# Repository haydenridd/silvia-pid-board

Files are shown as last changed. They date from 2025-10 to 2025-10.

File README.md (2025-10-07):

# Rancilio Silvia PID Board

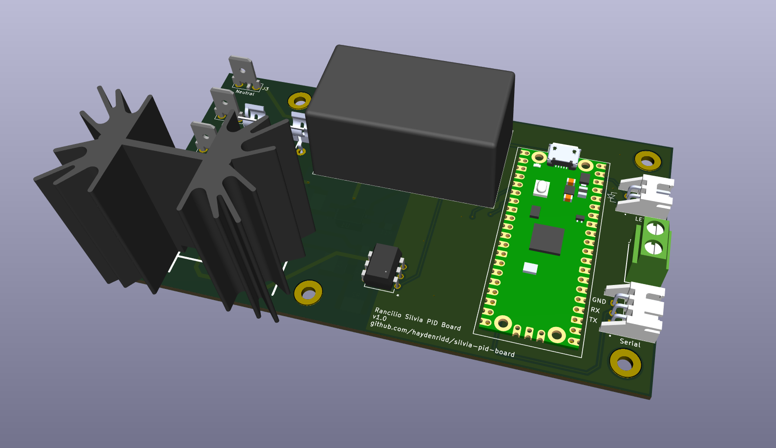
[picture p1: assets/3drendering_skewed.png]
rendering


A hardware and firmware project for adding PID boiler control to a stock Rancilio Silvia espresso machine.

## Obligatory Disclaimer

This project involves working with mains voltage as well as high power output heaters! Mains voltage *can kill or
seriously injure you* and improper control of an ~850W heating element *can start fires*. This project is provided
as-is with no regulatory certifications or guarantees of safety. It is on the user to do their due diligence in
ensuring their own safety, as well as the safe modification and operation of the espresso machine.

## Motivation

Adding PID heater control to the Rancilio Silvia is a popular mod, however it usually involves adding a
standalone PID controller like [this](https://www.auberins.com/index.php?main_page=product_info&products_id=36) to the
exterior of the machine. I've also seen a
number of great write-ups on home-brew mods \(so to speak\) like [this](https://misssilviapi.wordpress.com/) and
[this](https://int03.co.uk/blog/project-coffee-espiresso-machine/). However, many of the mods have
gravitated towards using various parts and modules found on Amazon, and are generally fairly invasive to the machine
itself (modules on the outside, cutting into the chassis, etc).

I had two goals with this project:
- Design a robust PID control board and source components entirely from a reputable distributor (DigiKey in this case)
- Design the board in such a way that it fits inside the machine, and leaves the control of the machine unchanged

### A Brief Aside on Amazon Parts
At the time of this writing, the electrical engineer in me would *not* consider Amazon to be a reputable retailer
for electronic parts. There have been many [reports](https://www.coffeeforums.co.uk/threads/gaggia-classic-pid-owners-watch-out-for-counterfeit-ssrs-on-ebay-amazon-etc.61314/)
of [fake parts](https://squashpractice.com/2024/01/01/counterfeits-parts-ebay-scammers-and-amazon-shills/) coming from
Amazon across all corners of industry. While these are generally ~half the price of the part they're
knocking off, you have essentially no recourse or accountability should this part fail in a catastrophic way. And
when it comes to switching AC mains and high powered heaters, that was not a gamble I was willing to take. This
project sources its parts entirely from DigiKey with the exception of a custom RTD sensor for the boiler.

## Design Ethos

I love the chunky, tactile feel of the stock Silvia machine. I wanted to leave how you control the machine entirely
unchanged. This is NOT a total conversion mod like the [Gagguino](https://gaggiuino.github.io/#/) although that project
is certainly cool. Post-mod, the machine still looks and functions largely the same to the external user, with a
small exception being how I use the heating lamp to indicate temperature status.

## Hardware Design

See [the hardware README](./silvia_pid_board/README.md) for a detailed breakdown of the electronic design, parts list,
and hookup diagram. This diagram shows the high-level design of the board:

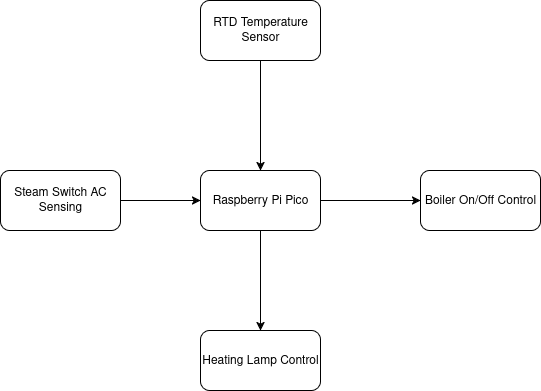
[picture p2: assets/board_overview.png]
board_overview


The board, in a hacky chip board "enclosure", fits snugly in between the steam valve and the leftmost control switches:
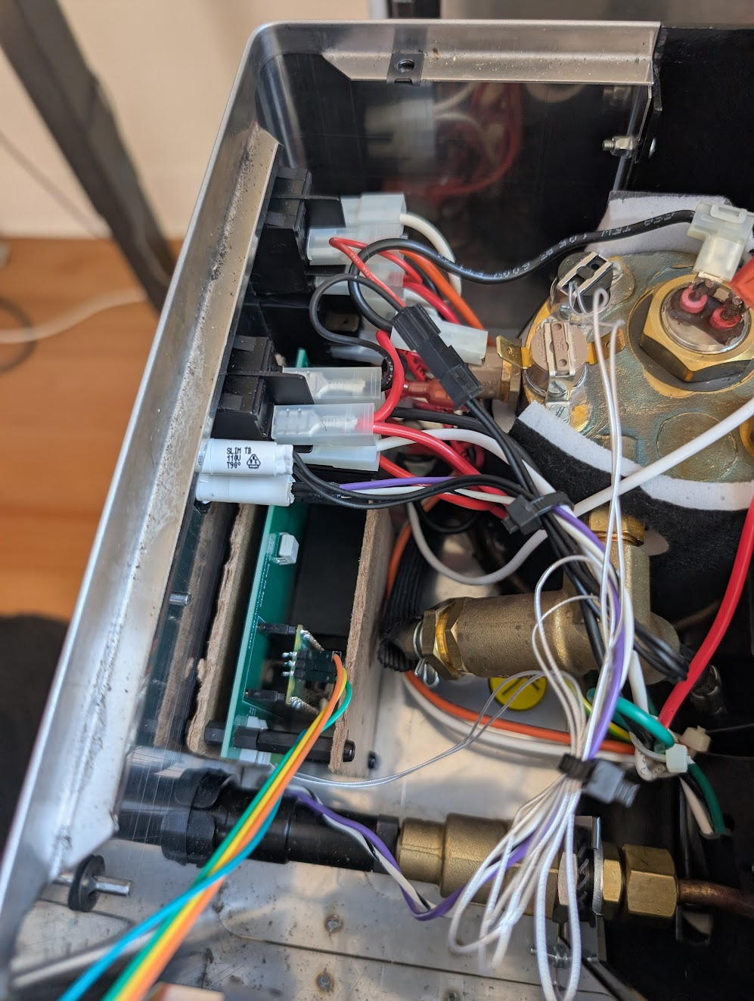
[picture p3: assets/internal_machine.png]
internal_machine


## Firmware Design

A Raspberry Pi Pico was used for the microcontroller driving the hardware because they're cheap, and extremely well
documented. The firmware is written in [Zig](https://ziglang.org/), a fantastic up-and-coming language that I've
fallen in love with for low-level firmware development. See [the firmware README](./firmware/README.md) for more
details.

## Performance

The following shows the temperature behavior of the thermostat style regulation that comes with a stock Silvia. 

A graph of temperature over time at the espresso temperature setpoint:

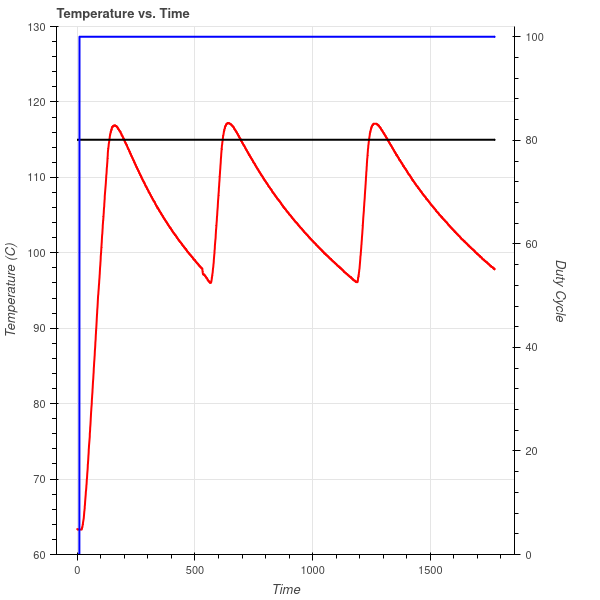
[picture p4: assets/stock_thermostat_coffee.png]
stock_coffee


And a graph of temperature of time at the steam temperature setpoint:

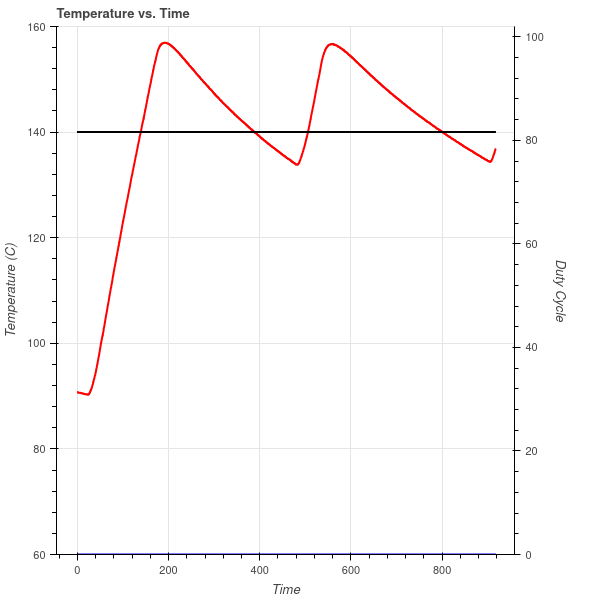
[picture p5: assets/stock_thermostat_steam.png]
stock_steam


Compare this to the new PID regulation at the espresso setpoint:

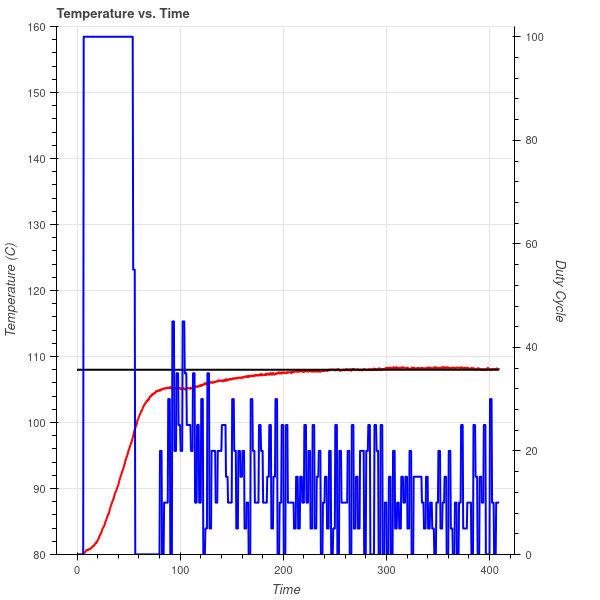
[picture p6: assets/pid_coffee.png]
pid_coffee


And regulation at the steam setpoint:

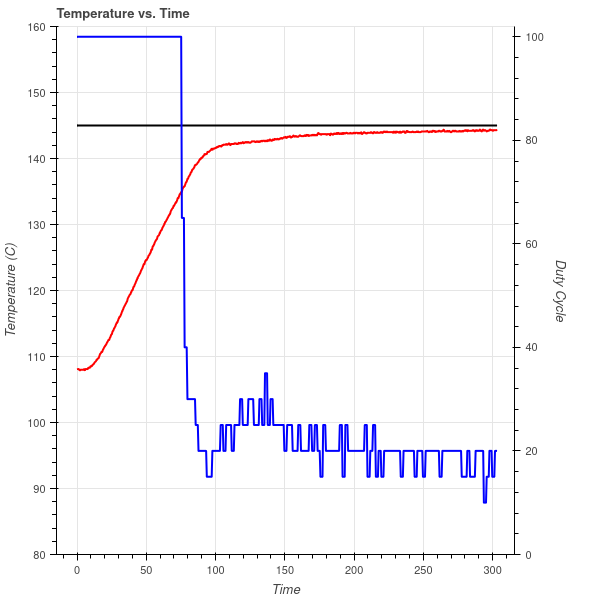
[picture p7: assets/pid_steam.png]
pid_steam


Where the red line is temperature, and the blue line is duty cycle of the heater. Both of these plots can be produced
with a [script](firmware/scripts/graph_temperature.py) in the firmware folder. See that README for more details on
data logging + plotting.

Espresso setpoint regulation is extremely tight, generally regulating to within 1C. Steam regulation generally sits
~2C below the setpoint of 145C, but experimentally I found this to produce nice milk steaming pressure. Both setpoints were chosen based
on the behavior of the original thermostat + some experimental tweaking. It should be noted temperature is measured
at the exterior of the boiler, meaning a setpoint of 108C does *not* mean 108C water is going through your
espresso puck. 

## Building Your Own

All the tools you need to make one of these modules yourself are provided in this repository. I used JLPCB to build the
boards, however the gerber files located in `silvia_pid_board/board_gerbers` can be used to build boards at a PCB
fab of your preference. Note though that design rules were checked according to JLPCB's capabilities. The KiCAD design
files are also available in `silvia_pid_board` should you want to modify the board or run different design rule checks.

At the time of writing, the total BOM cost of the Digikey parts is $34. Should you choose to use the same RTD module
costing $28, and JLPCB for your fab costing ~$30 with shipping, and add some cash for shipping from Digikey, the total
cost sits ~$100 for a buildout of this. Pretty good considering an off the shelf module is ~$150! I've included the 
Digikey part numbers with the [parts list](./silvia_pid_board/parts_list.csv) where relevant, so ordering parts for
this build should be fairly straightforward.

## Closing Thoughts and Areas of Improvement

This repo is unlikely to see any major updates, and mostly serves as a write-up/how-to for anyone looking to replicate
or expand upon this project. In its current state, it does exactly what I want for my machine. However, here are some
minor things I would change if I were to do another revision of the board/firmware:
- Add a standardized SWD header to the board + route corresponding signals from the Pico for easier debugger
connection
- Solder the RP2040 + required supporting ICs directly to the board to save space rather than using the Pico board
- Add CAD designs for a 3D printable enclosure
- Implement a serial port via a USB endpoint, removing the need for a dedicated UART connection
- Expand on the CLI and logging capabilities

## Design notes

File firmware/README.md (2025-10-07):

# PID Control Firmware

The following describes the firmware running on the Rpi Pico that implements PID control for the heater.

## Zig

The firmware is written in the [Zig](https://ziglang.org/) programming language, and currently tracks version `0.15.1`.
It uses the [MicroZig project](https://microzig.tech/) to provide a HAL and build utilities for the RP2040, a project
which I also contribute to!

## Building + Flashing

Installing Zig is required to build firmware. Once installed, build firmware by running `zig build` in this directory.
You will see two artifacts in `zig-out`. The `.elf` file can be flashed to the Pico over the SWD interface using a
debugger. There is an [example script](scripts/flash_fw.sh) that shows how this is accomplished with a JLink. The `.uf2`
file can be transferred to the Pico connected to a computer when it's in mass storage mode.

By default, the build occurs in debug mode. To build at higher optimization levels see `zig build -h`. 

## Architecture

The code follows a "super loop" architecture, with code seperated into modules that are given cpu time with the naming convention
`doWork()` as a method. Technically, this is known as "co-operative multitasking with static priority", where each module can't
get CPU cycles until the previous module yields control. The order in the loop each module is called can be thought
of as the "priority".

Examine the code for more details, but the high level modules are briefly described below.

### `Blink`

Blinks the on-board LED of the Pico at a fixed interval, as a sanity check that firmware hasn't crashed.

### `DataLogger`

Outputs CSV data points to a UART port for logging.

### `TemperatureRegulation`

Performs the PID control loop given regular temperature measurements from the RTD sensor. Setpoint is changed according to whether the steam switch is active or not.

### `RtdMeasurement`

Handles fetching temperature readings from the MAX31865 chip.

### `Cli`

Implements a rudimentary CLI for controlling firmware as it runs. Currently uses [RTT](https://kb.segger.com/RTT), however it is
designed in a way to take a generic `std.Io.Reader` as its input
source. A fun example of `comptime` usage to cut down on code repetition.

### `HeaterIndicator`

Controls the heater indicator LED using PWM. Currently it only has three states:
- Solid on: temperature is far enough away from target such that the boiler is turned on 100%
- Pulsing on: temperature is within a threshold to where PID is bringing temperature closer to target
- Solid off: Temperature is within 2C of target

Note that "solid on" still isn't at 100% duty cycle. I experimentally determined a nice value that seemed to match the brightness of the other lamps on the machine.

### `irq`

A special module that isn't "given work" like other modules, because
it entirely executes in interrupt handlers. Interrupts are used to
handle detecting regular zero crossing events on the pin that senses
whether or not the steam switch is turned on.

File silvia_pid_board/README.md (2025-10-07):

# Hardware Design

The following outlines:
- Board circuit design
- Hookup/wiring guide
- Board mounting
- BOM/Fabrication info

## Circuit Design

A PDF of the board schematic can be found [here](./silvia_pid_board.pdf), and is useful for following along with
circuit design discussion. The circuit design for this board can be broken into the following components:
- Power supply
- AC mains switching for the boiler
- AC mains detection from the steam switch
- Heating LED control

Note that this PCB was designed with a 120VAC/60Hz mains supply in mind, and that a careful design review should be
conducted if a user wants to adapt this to a different mains input (for instance 220VAC).  

### Power Supply

Extremely simple and easy, as it is a single component, the [IRM-05](https://www.meanwellusa.com/upload/pdf/IRM-05/IRM-05-spec.pdf).
While you could probably design a switched power supply that produces 5V from AC mains voltage for a little cheaper (this part costs $7),
this part simplified a lot of headaches. Does exactly as advertised, produces a clean 5V DC from 120 VAC delivering up
to 5W of power.

### AC Mains Switching

I spent the most time and intention on this part of the design, and switching AC to the boiler (to heat it) is
accomplished with the following circuit:
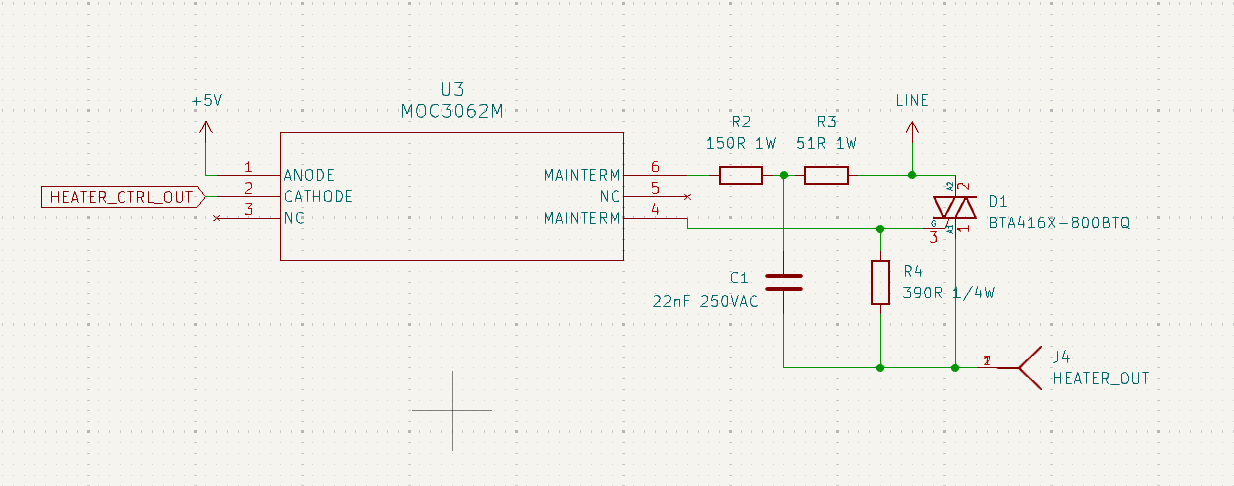
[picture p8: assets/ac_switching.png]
switching circuit


This was carefully designed based on the [following application note](https://www.st.com/resource/en/application_note/an5114-controlling-a-triac-with-a-phototriac-stmicroelectronics.pdf)
from ST Micro. I will be the first to admit it's over-engineered, as it almost certainly doesn't need a snubber circuit
given it's a simple resistive load being switched. One should note that the opto-coupler used is zero-crossing, meaning
no matter when the MCU goes to switch the heater on/off, it will only switch at the zero crossing point of the AC waveform.
Note you can only switch the heater on/off as fast as the frequency of the AC input (60Hz for US), however given the
duty period of the control loop is slow (one second) it doesn't matter.

The triac used for switching is passively cooled using a board mounted heatsink. Note that experimentally this has
been plenty effective for dissapating heat, but that a redesign is likely in order if switching a higher power heater
than the Silvia's.

### AC Mains Detection

This was entirely in service of allowing the steam switch to still turn on its own integrated AC powered lamp when it
switches on/off. The following circuit:
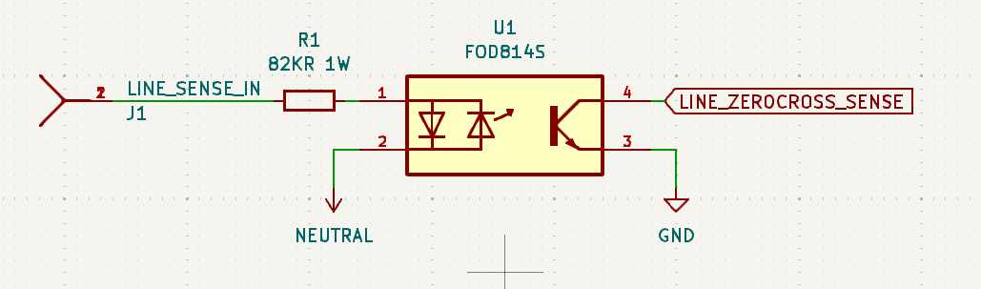
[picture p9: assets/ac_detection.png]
detection_circuit


Detects when the steam switch has been flipped "on" by detecting an AC signal. The [FOD814S](https://www.onsemi.com/download/data-sheet/pdf/fod814-d.pdf)
makes this quite easy. The `LINE_ZEROCROSS_SENSE` signal will end up being pulled to ground every time the AC signal
is over the turn-on voltage of the in-package photo-diodes. See the [firmware README](../firmware/README.md) for more
details on how this signal is used.

### Heating LED Control

The lower lamp on the power switched that is used as a heating indicator in the stock Silvia is replace by a white LED
controlled by the microcontroller. The dimensions of the chosen LED are quite similar to the stock lamp, so it was quite
easy to replace the stock lamp while preserving its housing and orange jewel lens. See the [firmware README](../firmware/README.md)
for more info on how this is used, but the general idea is a solid LED means "off target", a pulsing LED means
"close to target", and an off LED means "at target". 

## Hookup/Wiring Guide

The following is an annotated version of the electrical diagram provided with the Silvia's manual. It shows which
electrical connections have been removed or re-routed, and which signals they connect to on the PCB.
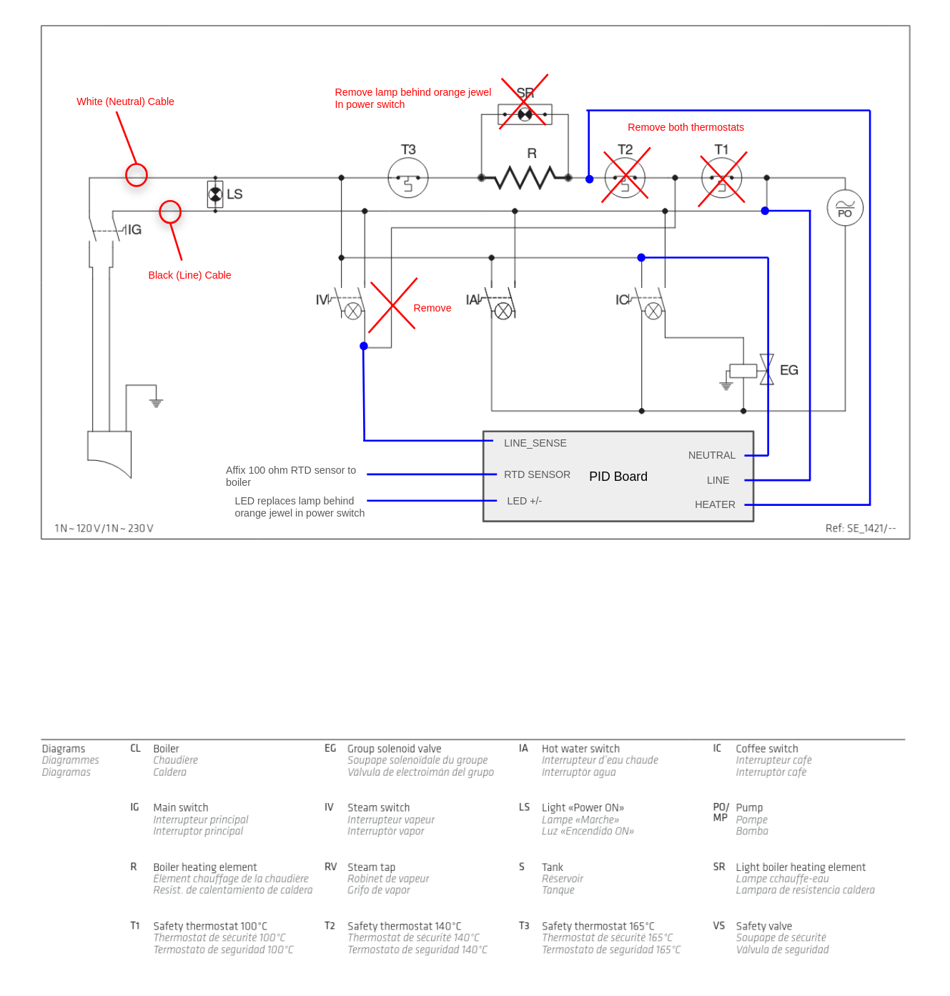
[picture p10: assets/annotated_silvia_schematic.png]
annotated_silvia_schematic


18 gauge wire was used for all AC signal level connections, and 22 gauge wire was used for all MCU signal
level connections (RTD sensor and LED).

## Board Mounting + Enclosure

Mounting holes are provided in the PCB to accomodate M3 size screws. I ended up using nylon standoffs and screws to
sandwich the board between two pieces of thick card-stock like material. 

## BOM/Fabrication

See [the following CSV](./parts_list.csv) for a full parts list for the project. The "Notes" column details whether the part goes on the
board itself, or is an ancillary part used for connections/etc.

The gerber files for getting this board fabricated are located in [board_gerbers](./board_gerbers), and pass the design
rules in `silvia_pid_board.kicad_dru` (provided by JLPCB).

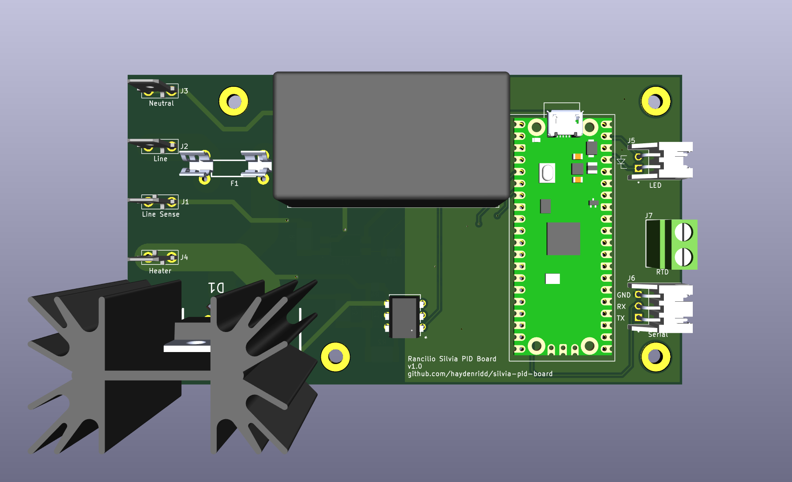
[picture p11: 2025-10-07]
assets/3drendering_top.png

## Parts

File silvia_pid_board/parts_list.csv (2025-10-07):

Reference | Value | Qty | DIGIKEY_PN | Notes
C1 | 22nF 250VAC | 1 | 399-CAN17C223KARACTUCT-ND | Board Component
C2,C3,C4 | 0.1uF | 3 | 311-1140-1-ND | Board Component
D1 | BTA416X-800BTQ | 1 | 1740-BTA416X-800BTQ-ND | Board Component
D1 | Heatsink | 1 | HS403-ND | Board Component
F1 | Fuse Holder | 1 | 36-3521-ND | Board Component
F1 | Fuse | 1 | 0225010.MXP-ND | Board Component
FB1 | FERRITE-0805NO | 1 | 490-1053-1-ND | Board Component
J1 | LINE_SENSE_IN | 1 | A29938CT-ND | Board Component
J2 | LINE_IN | 1 | A29938CT-ND | Board Component
J3 | NEUTRAL_IN | 1 | A29938CT-ND | Board Component
J4 | HEATER_OUT | 1 | A29938CT-ND | Board Component
J5 | S2B-XH-A | 1 | 455-S2B-XH-A-ND | Board Component
J6 | S3B-XH-A | 1 | 455-S3B-XH-A-ND | Board Component
J7 | 691137710002 | 1 | 732-10955-ND | Board Component
R1 | 82KR 1W | 1 | 13-RC2512JK-0782KLCT-ND | Board Component
R2 | 150R 1W | 1 | 13-SR2512JK-07150RLCT-ND | Board Component
R3 | 51R 1W | 1 | 13-AC2512JK-0751RLCT-ND | Board Component
R4 | 390R 1/4W | 1 | 311-390ERCT-ND | Board Component
R5 | 100R 1/4W | 1 | 311-270ERCT-ND | Board Component
R6,R8 | 100KR | 2 | 311-100KARCT-ND | Board Component
R7,R9,R12,R13,R14 | 10KR | 5 | 311-10KARCT-ND | Board Component
R10 | 270R 1/4W | 1 | 311-270ERCT-ND | Board Component
R11 | 6.2KR 1/4W | 1 | 311-6.2KERCT-ND | Board Component
R15 | 430Ω 0.1% | 1 | YAG1896CT-ND | Board Component
U1 | FOD814S | 1 | FOD814S-ND | Board Component
U2 | IRM-05-5 | 1 | 1866-3027-ND | Board Component
U3 | MOC3062M | 1 | MOC3062M-ND | Board Component
U4 | RASPBERRY_PI_PICO | 1 | 2648-SC0917-ND | Board Component
U5 | MBT3904DW1T1G | 1 | MBT3904DW1T1GOSCT-ND | Board Component
U6 | MAX31865AAP_ | 1 | MAX31865AAP+-ND | Board Component
~ | https://www.auberins.com/index.php?main_page=product_info&products_id=211 | 1 | ~ | Custom RTD sensor that fits in thermostat clip
~ | XHP-2 | 1 | 455-2266-ND | 2 position connector for RTD sensor port
~ | XHP-3 | 1 | 455-2219-ND | 3 position connector for UART port
~ | 2-520263-2 | 4 | A27821CT-ND | AMP connectors for connecting AC signals to board
~ | PPPC201LFBN-RC | 2 | S7053-ND | Female headers for Rpi Pico
~ | SXH-001T-P0.6N | 5 | 455-4220-100-ND | Crimp connectors
~ | INL-3AW30 | 1 | 1830-1006-ND | White LED for temperature lamp indicator replacement

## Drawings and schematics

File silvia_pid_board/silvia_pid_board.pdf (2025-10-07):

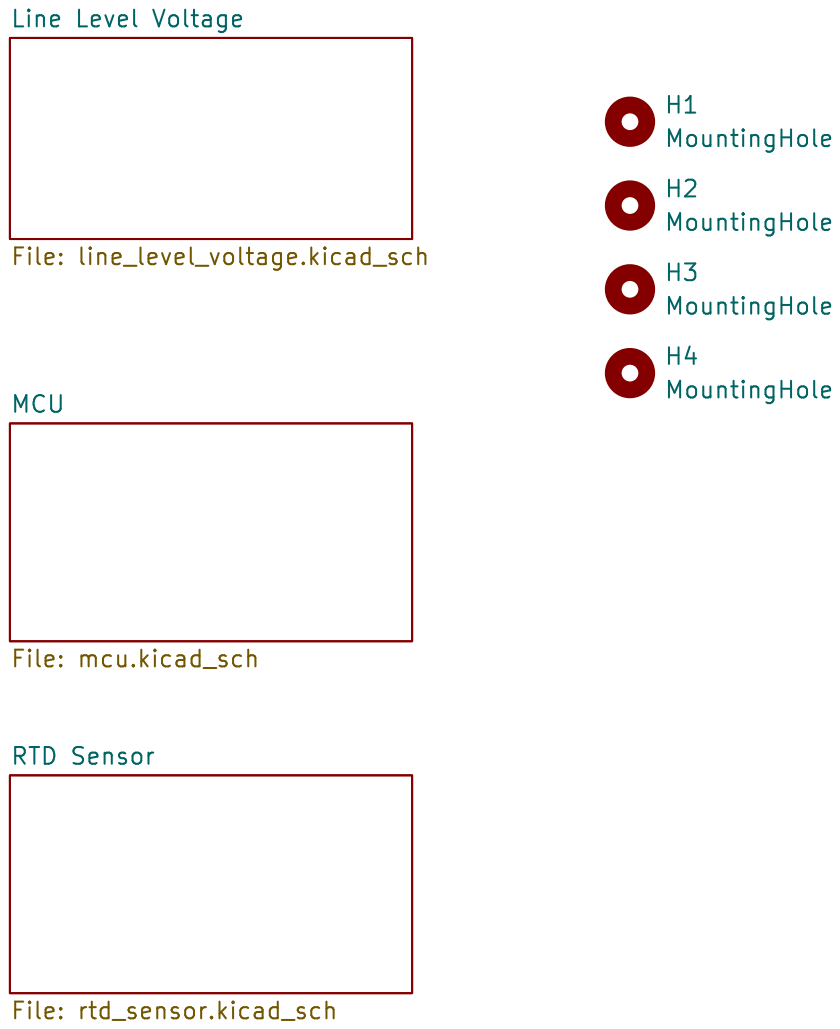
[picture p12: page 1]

Line Level Voltage File: line_level_voltage.kicad_sch RTD Sensor File: rtd_sensor.kicad_sch MCU

File: silvia_pid_board.kicad_sch Sheet: /
Id: 1/4 Title: Rancilio Silvia PID Board

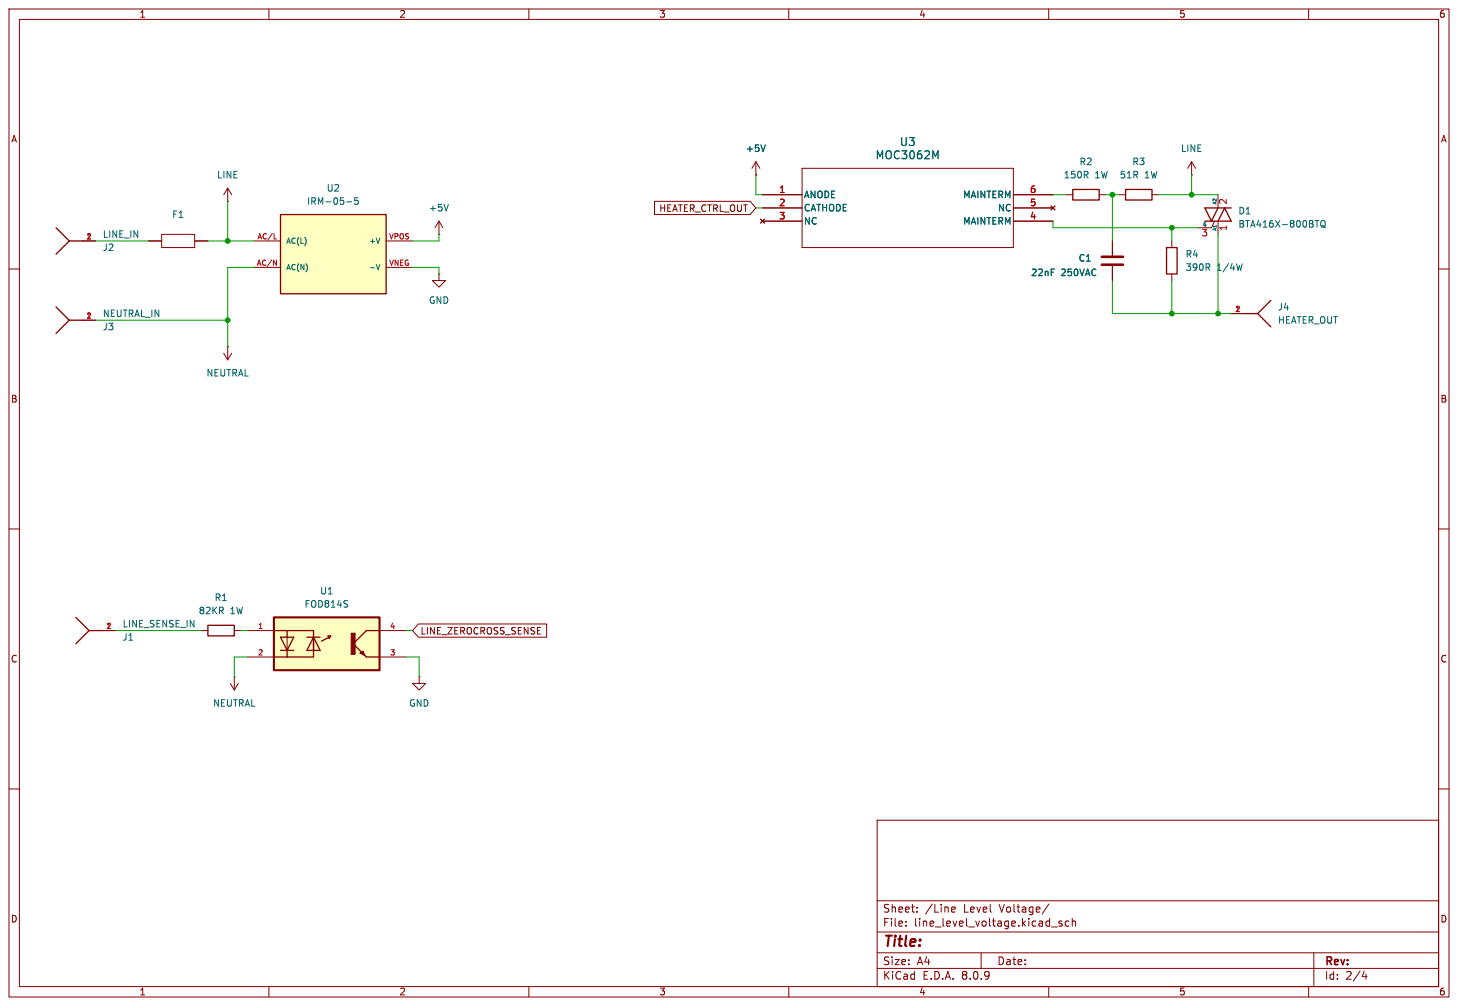
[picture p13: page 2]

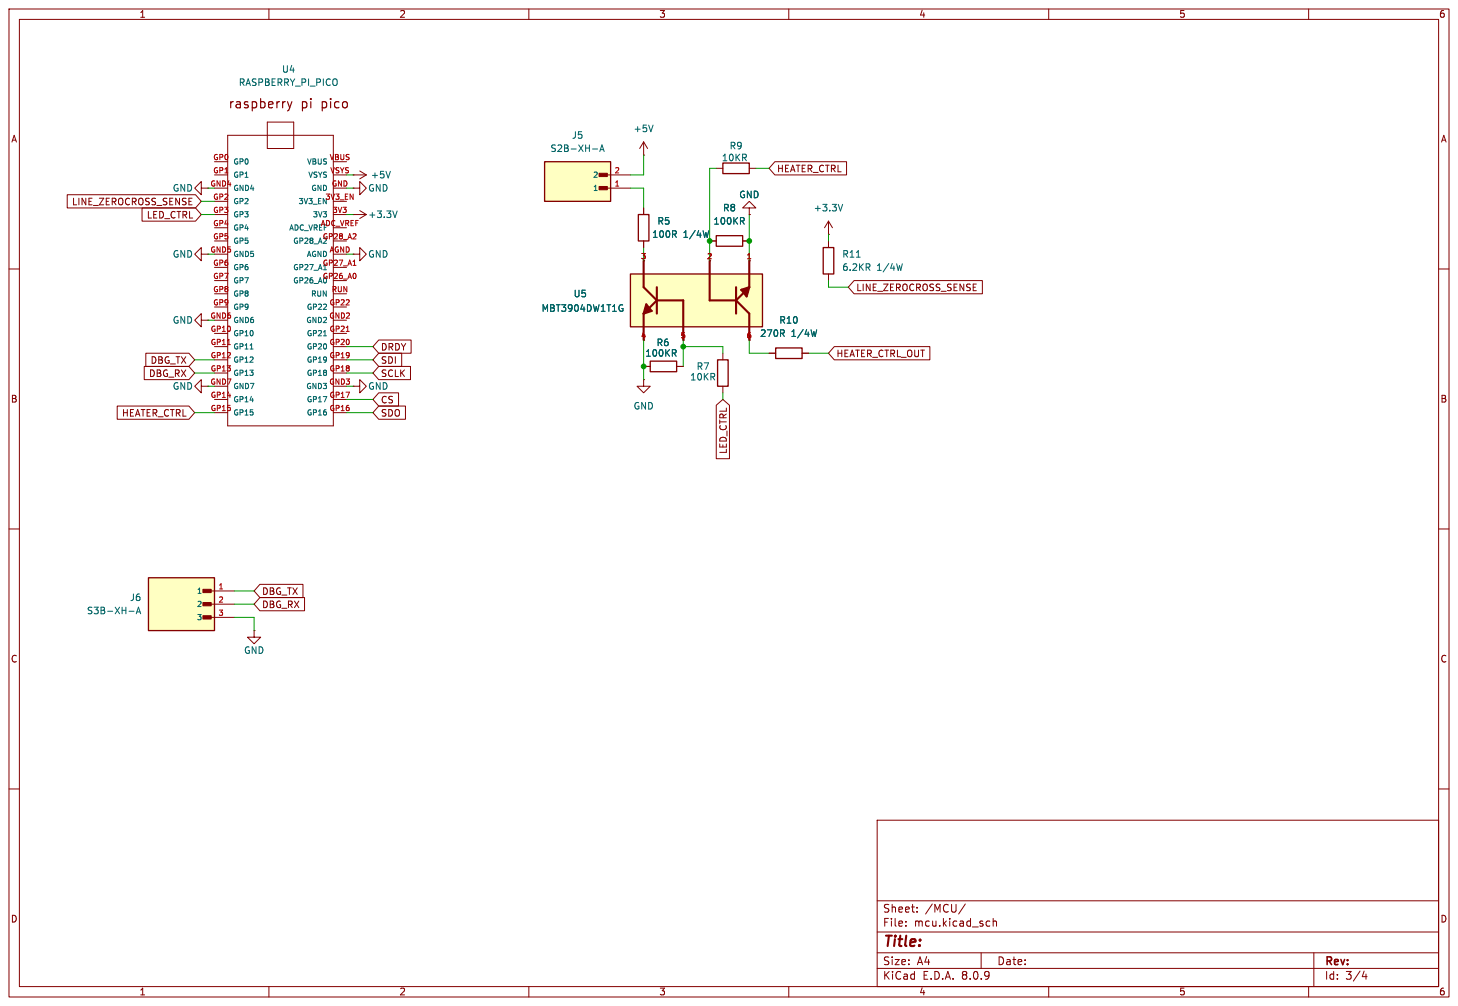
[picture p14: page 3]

Id: 3/4 Title: File: mcu.kicad_sch Sheet: /MCU/

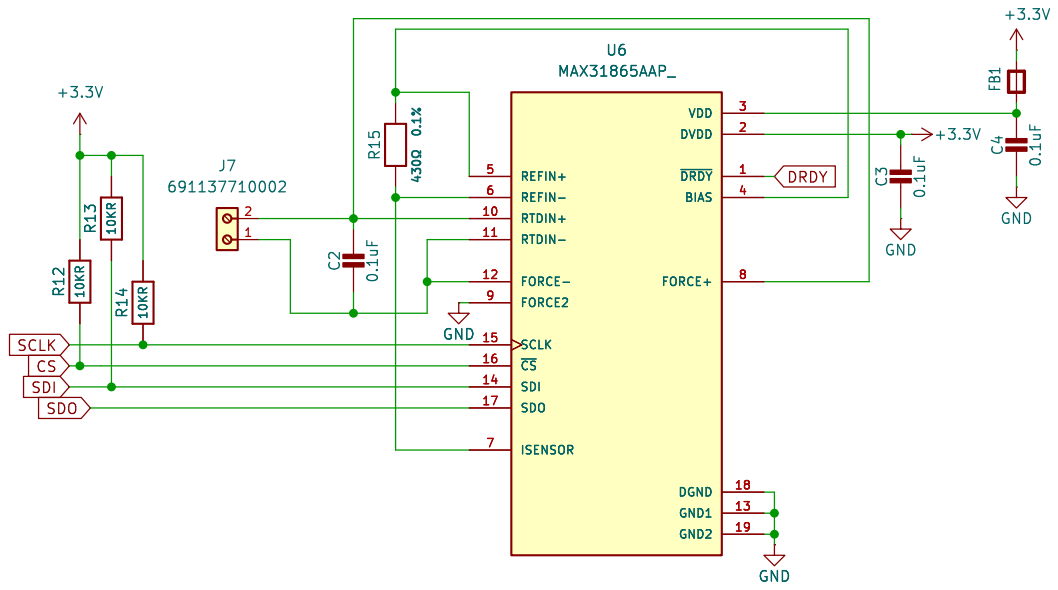
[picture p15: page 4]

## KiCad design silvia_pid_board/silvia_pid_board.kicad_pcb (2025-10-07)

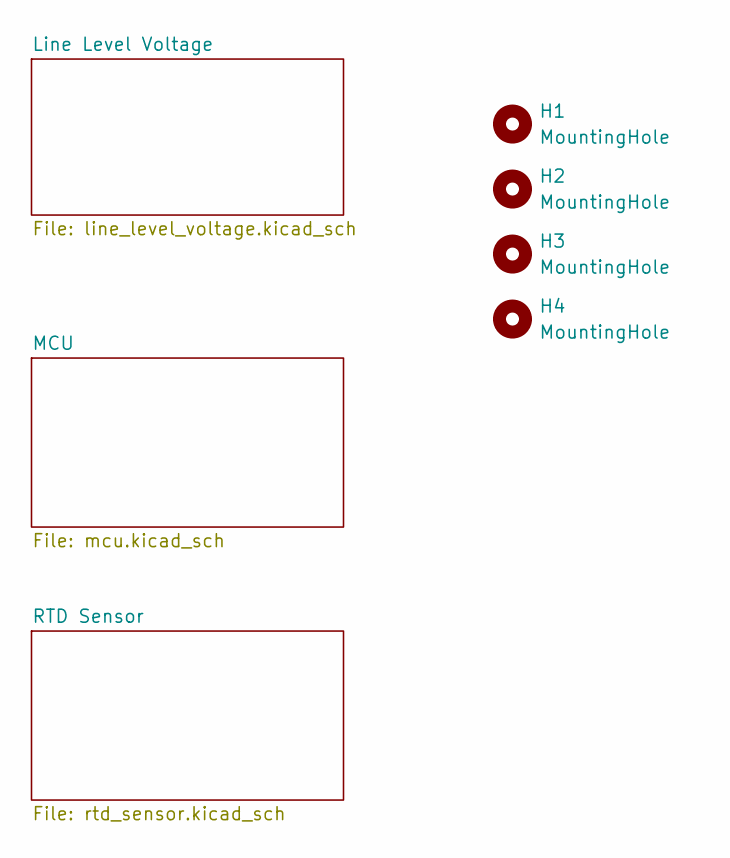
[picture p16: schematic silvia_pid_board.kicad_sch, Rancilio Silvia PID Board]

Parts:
H1, H2, H3, H4: MountingHole; MountingHole_3.2mm_M3_Pad_TopOnly

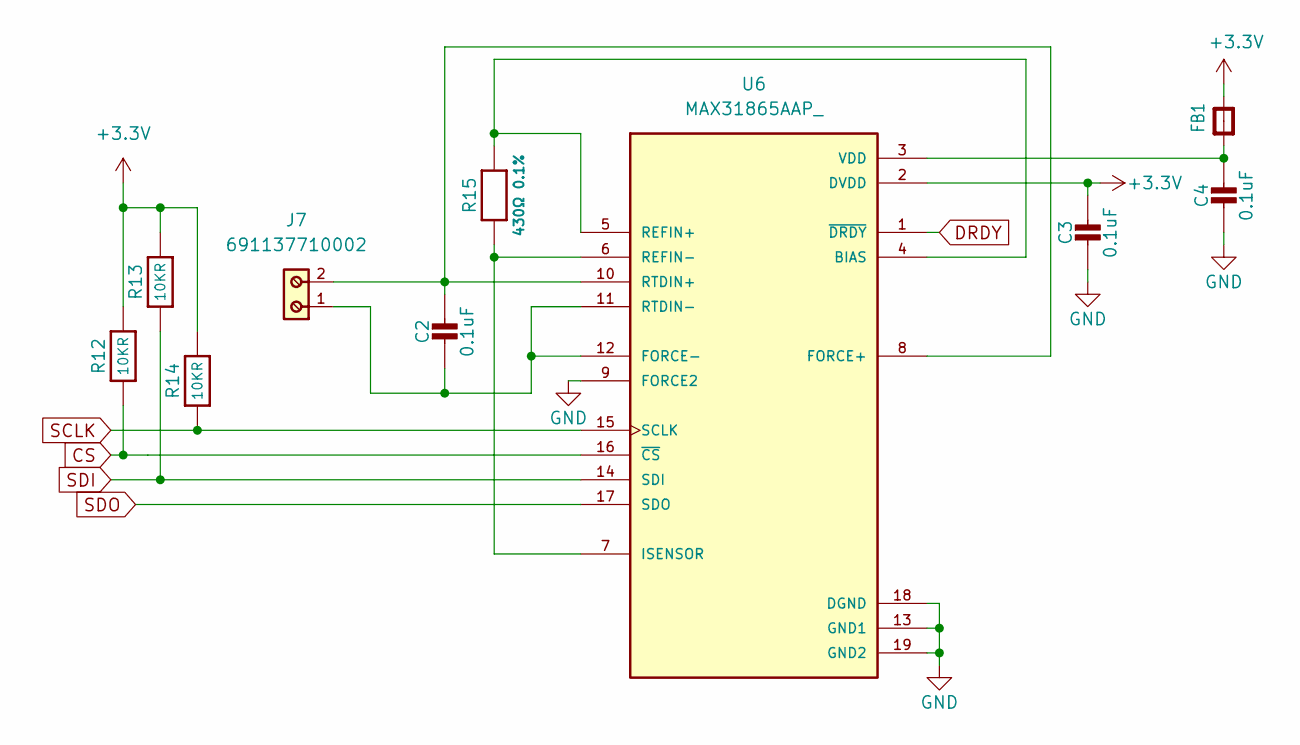
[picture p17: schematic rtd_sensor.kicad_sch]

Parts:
C2, C3, C4: 0.1uF; C_0805_2012Metric_Pad1.18x1.45mm_HandSolder; DIGIKEY_PN 311-1140-1-ND
FB1: FERRITE-0805NO; R_0805_2012Metric_Pad1.20x1.40mm_HandSolder; DIGIKEY_PN 490-1053-1-ND
J7: 691137710002; DIGIKEY_PN 732-10955-ND
R12, R13, R14: 10KR; R_0805_2012Metric_Pad1.20x1.40mm_HandSolder; DIGIKEY_PN 311-10KARCT-ND
R15: 430Ω 0.1%; R_0805_2012Metric_Pad1.20x1.40mm_HandSolder; DIGIKEY_PN YAG1896CT-ND
U6: MAX31865AAP_; SOP65P777X199-20N; DIGIKEY_PN MAX31865AAP+-ND

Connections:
+3.3V: C3.1, FB1.2, R12.2, R13.2, R14.2, U6.2 (DVDD); also elsewhere on the board
CS: R12.1, U6.16 (~CS); also elsewhere on the board
DRDY: U6.1 (~DRDY); also elsewhere on the board
GND: C3.2, C4.2, U6.9 (FORCE2), U6.13 (GND1), U6.18 (DGND), U6.19 (GND2); also elsewhere on the board
unnamed: C4.1, FB1.1, U6.3 (VDD)
unnamed: R15.2, U6.4 (BIAS), U6.5 (REFIN+)
unnamed: C2.1, J7.2, U6.8 (FORCE+), U6.10 (RTDIN+)
unnamed: C2.2, J7.1, U6.11 (RTDIN-), U6.12 (FORCE-)
unnamed: R15.1, U6.6 (REFIN-), U6.7 (ISENSOR)
SCLK: R14.1, U6.15 (SCLK); also elsewhere on the board
SDI: R13.1, U6.14 (SDI); also elsewhere on the board
SDO: U6.17 (SDO); also elsewhere on the board

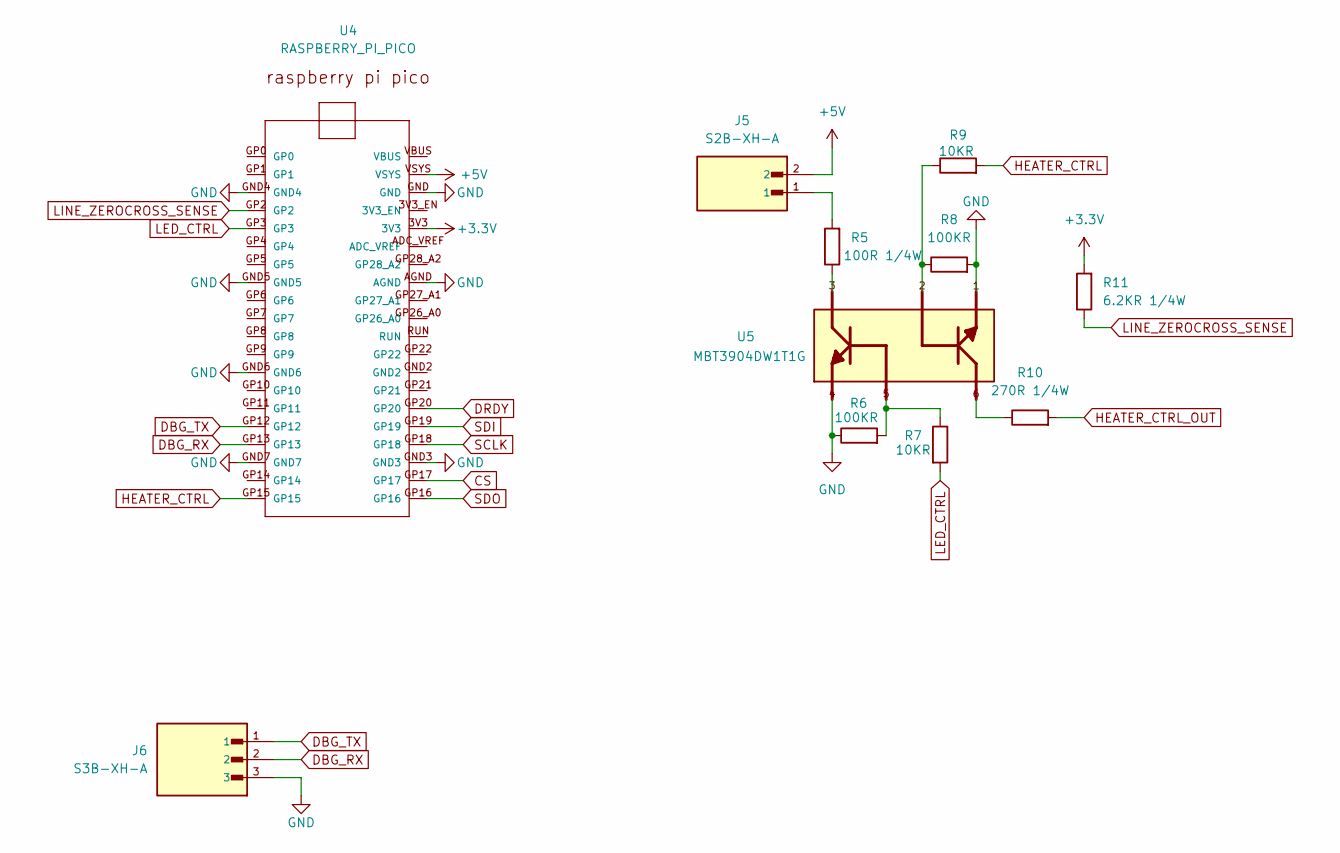
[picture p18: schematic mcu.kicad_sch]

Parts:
J5: S2B-XH-A; JST_S2B-XH-A; DIGIKEY_PN 455-S2B-XH-A-ND
J6: S3B-XH-A; JST_S3B-XH-A; DIGIKEY_PN 455-S3B-XH-A-ND
R5: 100R 1/4W; R_1206_3216Metric_Pad1.30x1.75mm_HandSolder; DIGIKEY_PN 311-270ERCT-ND
R6, R8: 100KR; R_0805_2012Metric_Pad1.20x1.40mm_HandSolder; DIGIKEY_PN 311-100KARCT-ND
R7, R9: 10KR; R_0805_2012Metric_Pad1.20x1.40mm_HandSolder; DIGIKEY_PN 311-10KARCT-ND
R10: 270R 1/4W; R_1206_3216Metric_Pad1.30x1.75mm_HandSolder; DIGIKEY_PN 311-270ERCT-ND
R11: 6.2KR 1/4W; R_1206_3216Metric_Pad1.30x1.75mm_HandSolder; DIGIKEY_PN 311-6.2KERCT-ND
U4: RASPBERRY_PI_PICO; DIGIKEY_PN S7053-ND(sockets),2648-SC0917-ND(pico)
U5: MBT3904DW1T1G; SOT236; DIGIKEY_PN MBT3904DW1T1GOSCT-ND

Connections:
+3.3V: R11.2, U4.3V3; also elsewhere on the board
+5V: J5.2, U4.VSYS; also elsewhere on the board
CS: U4.GP17; also elsewhere on the board
DBG_RX: J6.2, U4.GP13
DBG_TX: J6.1, U4.GP12
DRDY: U4.GP20; also elsewhere on the board
GND: J6.3, R6.1, R8.2, U4.AGND, U4.GND, U4.GND3, U4.GND4, U4.GND5, U4.GND6, U4.GND7, U5.1, U5.4; also elsewhere on the board
HEATER_CTRL: R9.2, U4.GP15
HEATER_CTRL_OUT: R10.2; also elsewhere on the board
LED_CTRL: R7.2, U4.GP3
LINE_ZEROCROSS_SENSE: R11.1, U4.GP2; also elsewhere on the board
unnamed: J5.1, R5.2
unnamed: R5.1, U5.3
unnamed: R6.2, R7.1, U5.5
unnamed: R8.1, R9.1, U5.2
unnamed: R10.1, U5.6
SCLK: U4.GP18; also elsewhere on the board
SDI: U4.GP19; also elsewhere on the board
SDO: U4.GP16; also elsewhere on the board

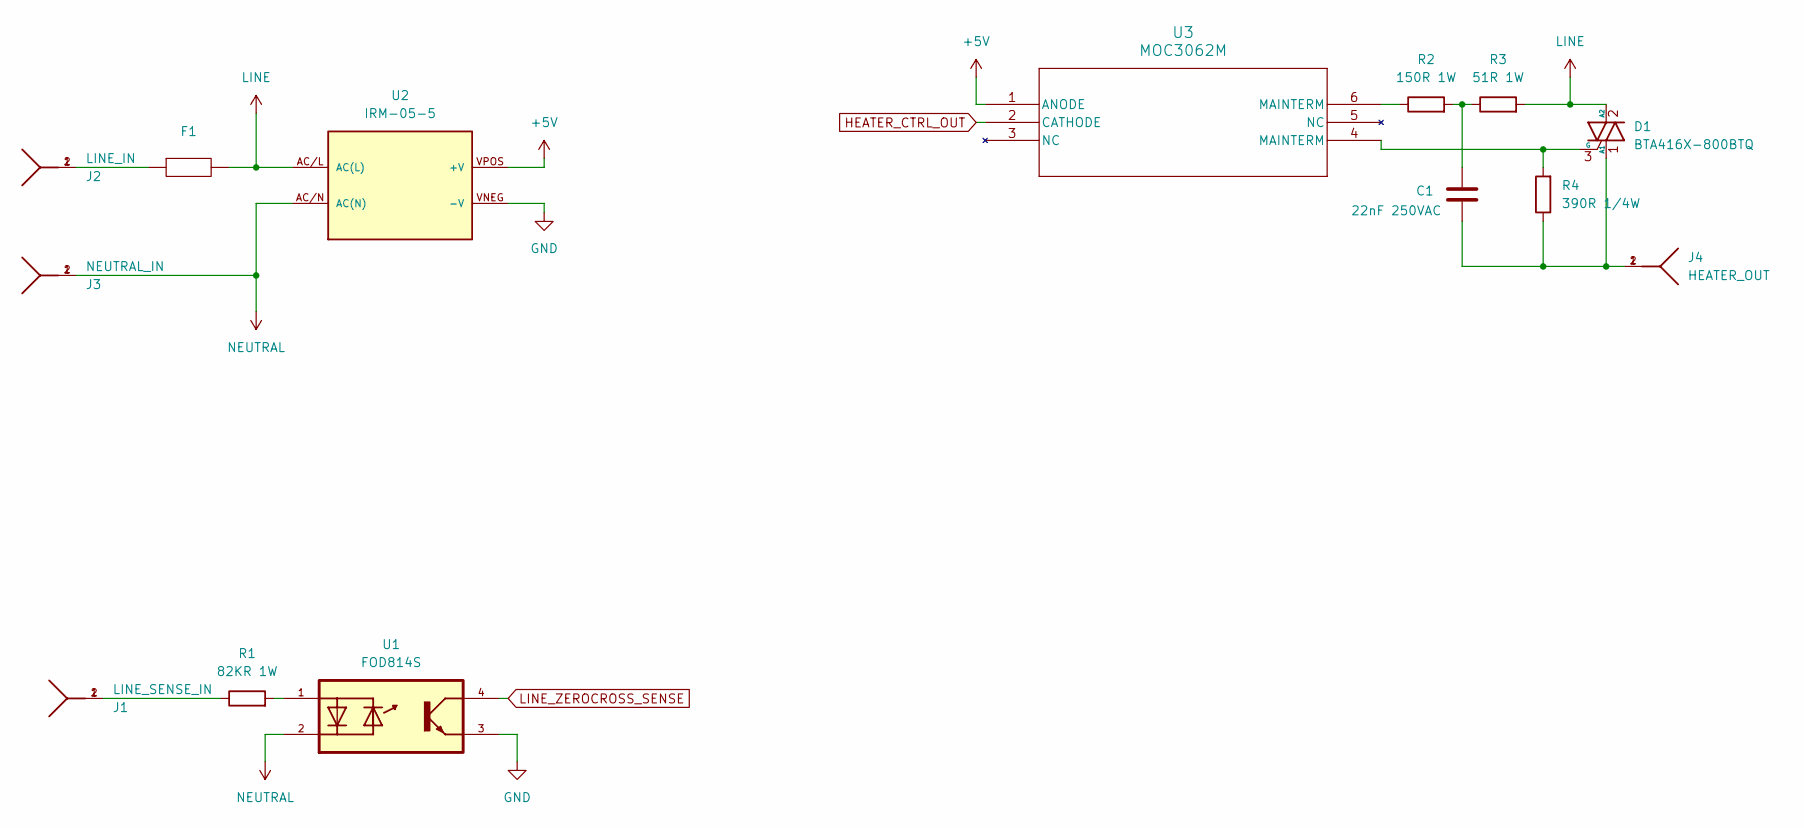
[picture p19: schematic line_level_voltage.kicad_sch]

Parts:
C1: 22nF 250VAC; C_1808_4520Metric_Pad1.72x2.30mm_HandSolder; PARTREV 11-Oct-17; DIGIKEY_PN 399-CAN17C223KARACTUCT-ND
D1: BTA416X-800BTQ; to220_with_heatsink; DIGIKEY_PN 1740-BTA416X-800BTQ-ND(Triac), HS403-ND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
F1: fuse_holder; DIGIKEY_PN 36-3521-ND (Holders),0225010.MXP-ND (Fu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
J1: LINE_SENSE_IN; CONN_63824-1; PARTREV R; DIGIKEY_PN A29938CT-ND
J2: LINE_IN; CONN_63824-1; PARTREV R; DIGIKEY_PN A29938CT-ND
J3: NEUTRAL_IN; CONN_63824-1; PARTREV R; DIGIKEY_PN A29938CT-ND
J4: HEATER_OUT; CONN_63824-1; PARTREV R; DIGIKEY_PN A29938CT-ND
R1: 82KR 1W; R_2512_6332Metric_Pad1.40x3.35mm_HandSolder; DIGIKEY_PN 13-RC2512JK-0782KLCT-ND
R2: 150R 1W; R_2512_6332Metric_Pad1.40x3.35mm_HandSolder; DIGIKEY_PN 13-SR2512JK-07150RLCT-ND
R3: 51R 1W; R_2512_6332Metric_Pad1.40x3.35mm_HandSolder; DIGIKEY_PN 13-AC2512JK-0751RLCT-ND
R4: 390R 1/4W; R_1206_3216Metric_Pad1.30x1.75mm_HandSolder; DIGIKEY_PN 311-390ERCT-ND
U1: FOD814S; SOIC254P1016X385-4N; DIGIKEY_PN FOD814S-ND
U2: IRM-05-5; CONV_IRM-05-5; DIGIKEY_PN 1866-3027-ND
U3: MOC3062M; PDIP6_8P89X6P6_ONS; DIGIKEY_PN MOC3062M-ND

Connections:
+5V: U2.VPOS (+V), U3.1 (ANODE); also elsewhere on the board
GND: U1.3, U2.VNEG (-V); also elsewhere on the board
HEATER_CTRL_OUT: U3.2 (CATHODE); also elsewhere on the board
LINE: D1.2 (A2), F1.3, F1.4, R3.2, U2.AC/L (AC(L))
LINE_ZEROCROSS_SENSE: U1.4; also elsewhere on the board
NEUTRAL: J3.1, J3.2, U1.2, U2.AC/N (AC(N))
unnamed: C1.1, R2.2, R3.1
unnamed: C1.2, D1.1 (A1), J4.1, J4.2, R4.1
unnamed: D1.3 (G), R4.2, U3.4 (MAINTERM)
unnamed: F1.1, F1.2, J2.1, J2.2
unnamed: J1.1, J1.2, R1.1
unnamed: R1.2, U1.1
unnamed: R2.1, U3.6 (MAINTERM)

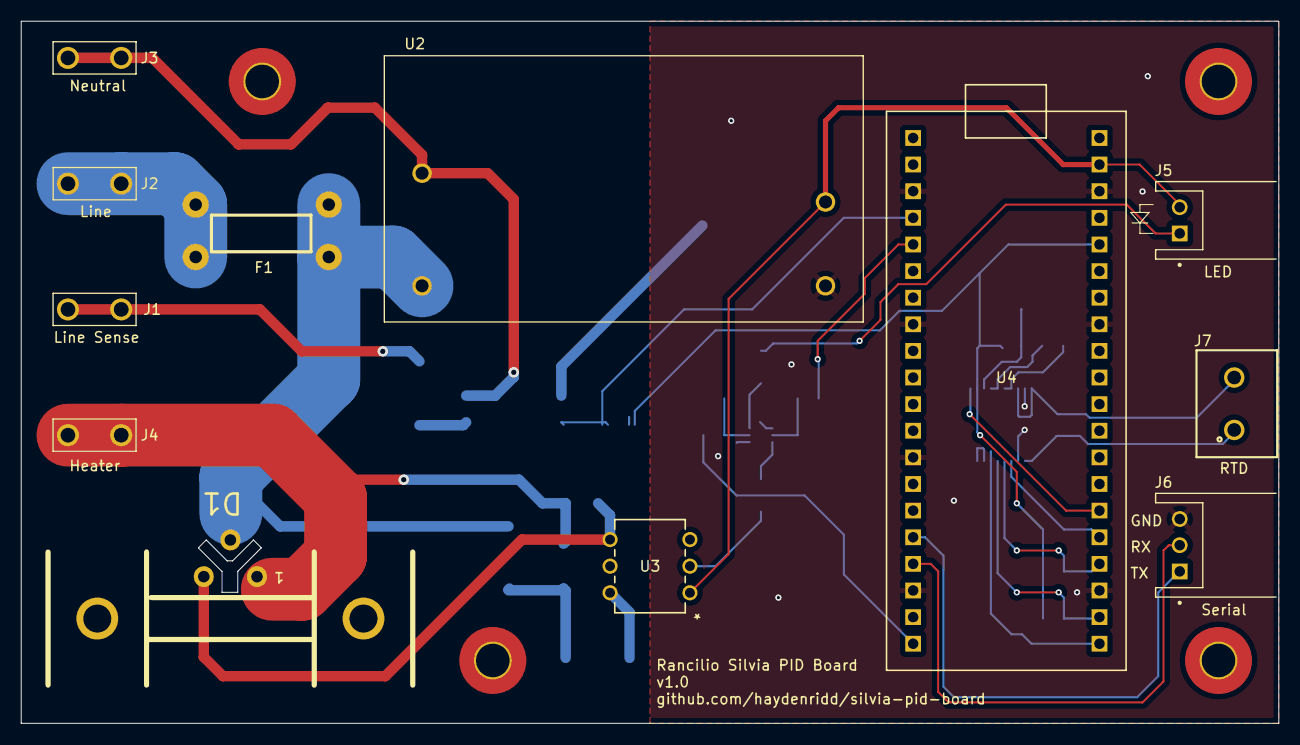
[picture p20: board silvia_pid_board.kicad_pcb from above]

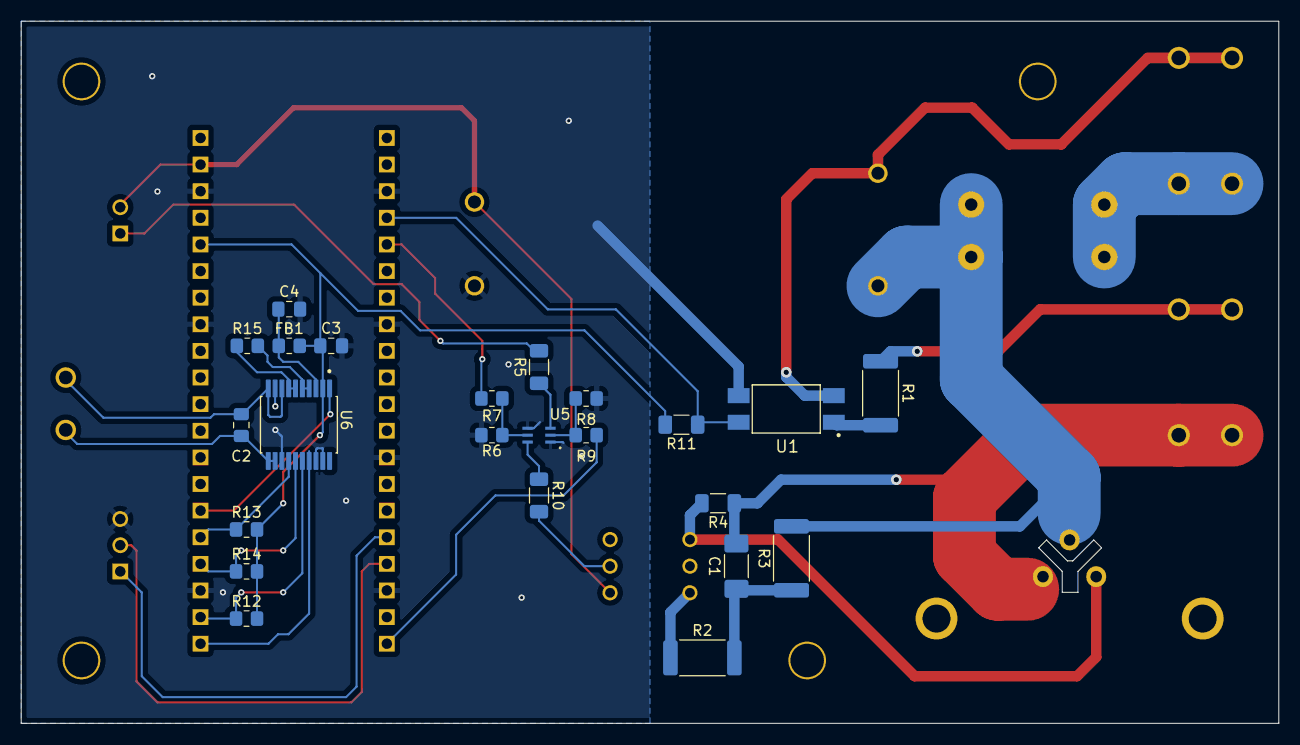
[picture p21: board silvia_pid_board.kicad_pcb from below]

Board: 2 copper layers, 120.0 x 67.0 mm, 39 parts (23 on the bottom side), 33 nets.

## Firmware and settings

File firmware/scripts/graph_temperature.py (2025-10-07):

import serial
import bokeh
from bokeh.models import LinearAxis, Range1d, Legend, ColumnDataSource
from bokeh.io import curdoc
from bokeh.plotting import figure
import time
import datetime


ser = serial.Serial("/dev/serial/by-id/usb-FTDI_FT232R_USB_UART_AB0MN1QY-if00-port0", 115200, timeout=1)

temp_ds = ColumnDataSource(data = {"Temperature": [], "Time": []})
dc_ds = ColumnDataSource(data = {"Duty Cycle": [], "Time": []})
setpoint_ds = ColumnDataSource(data = {"Set Point": [], "Time": []})
init_ts = datetime.datetime.now().timestamp()

def callback():
    global temp_ds
    global dc_ds
    global init_ts
    global ser
    try:
        ln = ser.readline().decode("utf-8")
        ls = ln.strip().split(",")
        time_val = datetime.datetime.now().timestamp() - init_ts
        temp_ds.stream({"Temperature": [float(ls[0])], "Time": [time_val]})
        dc_ds.stream({"Duty Cycle": [float(ls[1])], "Time": [time_val]})
        setpoint_ds.stream({"Set Point": [float(ls[2])], "Time": [time_val]})
    except Exception as e:
        print("Error reading data point: ", e)
        pass


p = figure(title="Temperature vs. Time", x_axis_label="Time", y_axis_label="Temperature (C)")
p.line(x="Time", y="Temperature", line_width=2, source=temp_ds, color="red")
p.line(x="Time", y="Set Point", line_width=2, source=setpoint_ds, color="black")
p.y_range = Range1d(80, 160)
p.extra_y_ranges["duty_range"] = Range1d(0, 102)
ax2 = LinearAxis(y_range_name="duty_range", axis_label="Duty Cycle")
p.add_layout(ax2, "right")
p.line(x="Time", y="Duty Cycle", line_width=2, source=dc_ds, color="blue", y_range_name="duty_range")

curdoc().add_periodic_callback(callback, 100)
curdoc().add_root(p)

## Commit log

2025-10-07 - Upload project
    [high_voltage.kicad_sch, line_level_voltage.kicad_sch, low_voltage.kicad_sch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]
2025-10-07 - Added gerber files
    [silvia_pid_board-B_Cu.gbr, silvia_pid_board-B_Mask.gbr, silvia_pid_board-B_Paste.gbr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]
2025-10-07 - Added schematic pdf
2025-10-07 - Small clarification on temperature regulation
